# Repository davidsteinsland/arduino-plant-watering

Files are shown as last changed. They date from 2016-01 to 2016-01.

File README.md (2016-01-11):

Arduino Plant Watering
======================

A Real Time Clock controlled water pump regulator, for watering your plants.
The LCD have four available states:

- Initial state: Shows the time and how many times the pump has ran
- Pump configuration: Configure how many seconds the pump will run
- Schedule configuration: Enable/disable the timer
- Alarm configuration: Configure the time between each watering (can be every minute; a specific minute every hour; or a specific time each day).

The internal software is using a mixture of the RTC module and AVR's Watchdog Timer to properly time the pump and the schedule.
A float switch is also connected to the circuit, allowing the pump to run if there is enough water. It will also cut-off the pump as soon
as float switch turns off.

The power supply is a 12v wall-wart that's fused with 50mA to Arduino and 5A to the pump.

The three buttons are regulated at 0V, 1V and 2V, and read using `A0`. The switches are debounced in software.

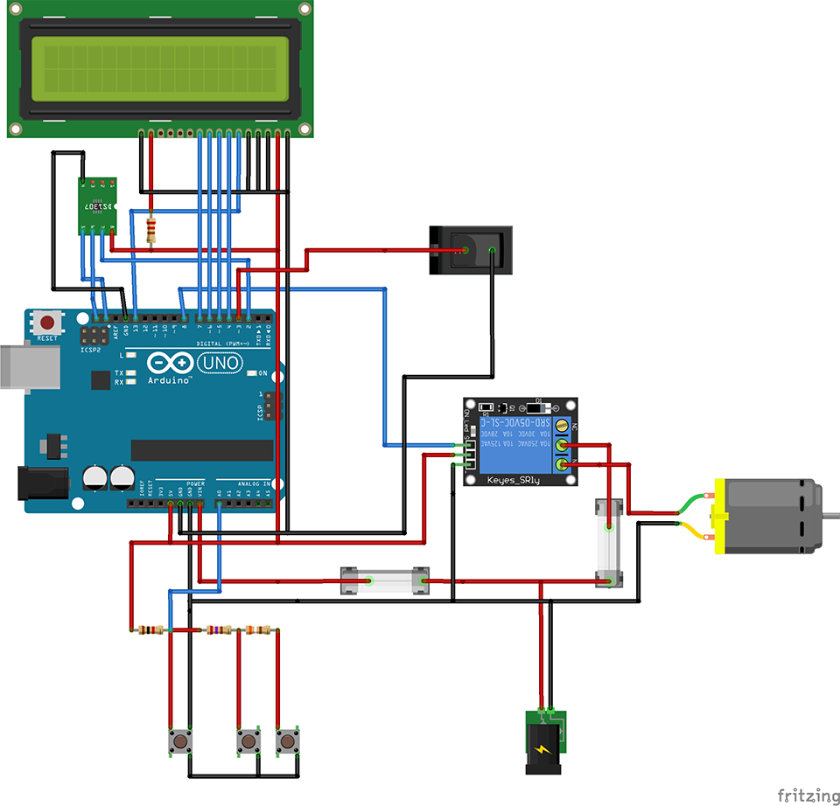
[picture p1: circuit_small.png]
Circuit


# Hardware

* [12V relay module](http://www.kjell.com/se/sortiment/el/elektronik/arduino/moduler/relamodul-for-arduino-p87878)
* [Water hose](http://www.biltema.no/no/Bil---MC/Bilreservedeler/Viskerutstyr/Spylerpumpe/Spylerpumpe-ovrig/Spylerslange-5-m-2000031910/)
* [Windshield washer pump](http://www.biltema.no/no/Bil---MC/Bilreservedeler/Viskerutstyr/Spylerpumpe/Spylerpumpe/Vindusspylerpumpe-universal-2000017965/)
* [12V power supply](http://www.biltema.no/no/Kontor---Teknikk/Batteri-og-Stromforsyning/Nettaggregat-og-ladere/Nettadapter-2000022525/)
* [16x2 LCD](http://hobbykomponenter.no/elektronikk/komponenter/display/lcd/16-and-215-2-lcd-display-blaa/)
* [DS3231 RTC module](http://hobbykomponenter.no/elektronikk/moduler/ds3231-rtc-modul/) (or similar)
* [Float switch](http://hobbykomponenter.no/elektronikk/sensorer/nivaasensor-sidemontert-flottr/)

## Additional

* Resistors
* Wires
* LEDs
* A switch button
* Free time.

# Future improvements

- Flowmeter: Configure the amount of water your want to be pumped, instead of pump time
- Hardware debouncing of buttons
- Noise reducing of water pump when it's active
- Status LEDs
- Bluetooth / integration with the nRF51 kit by Nordic Semiconductor.

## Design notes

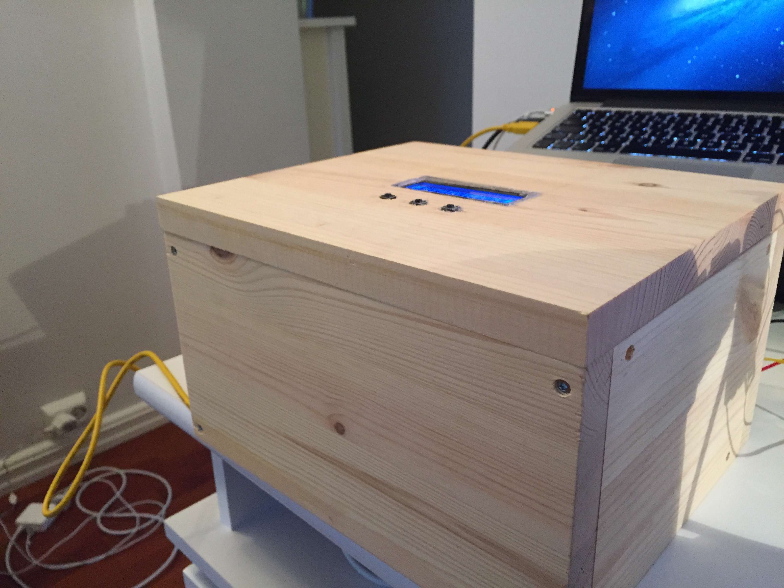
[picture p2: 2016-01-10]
photos/v2/box_side.jpg

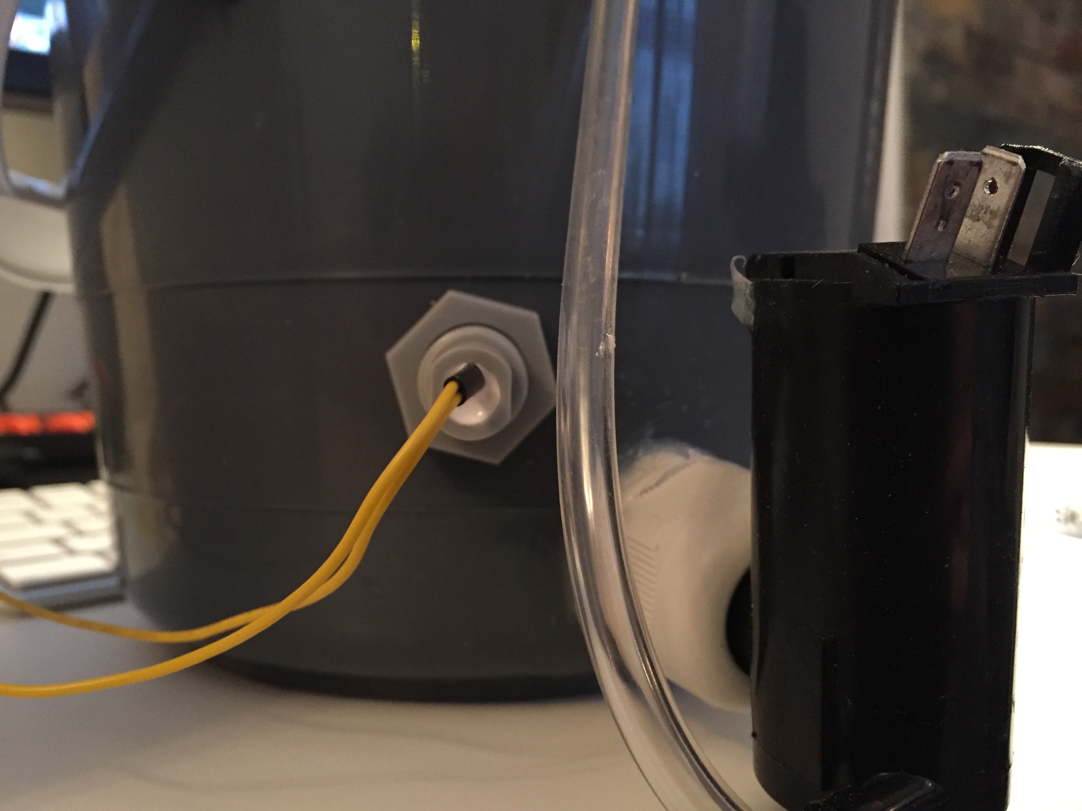
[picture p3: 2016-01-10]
photos/v2/bucket_pump.jpg

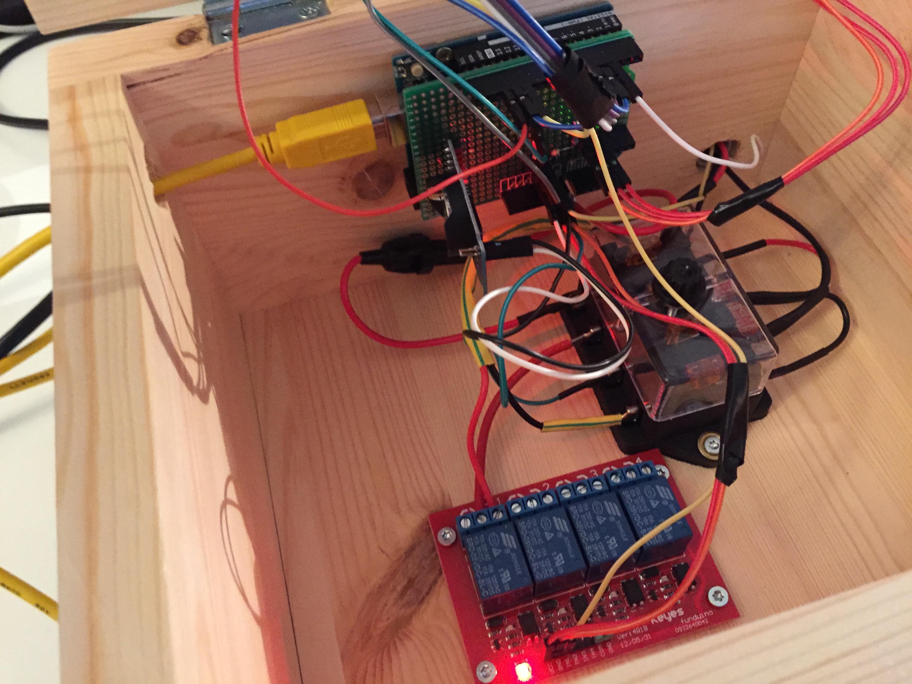
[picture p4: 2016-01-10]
photos/v2/inside_1.jpg

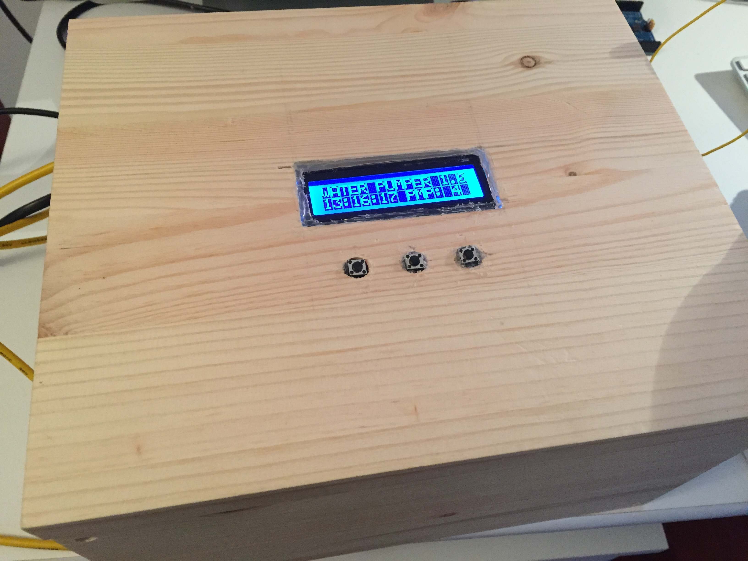
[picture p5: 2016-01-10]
photos/v2/box.jpg

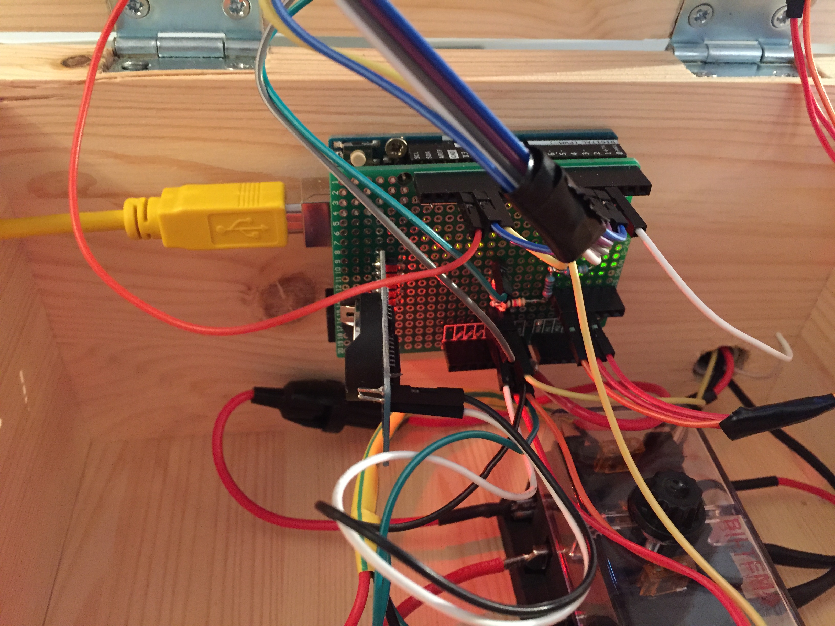
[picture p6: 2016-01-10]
photos/v2/inside_2.jpg

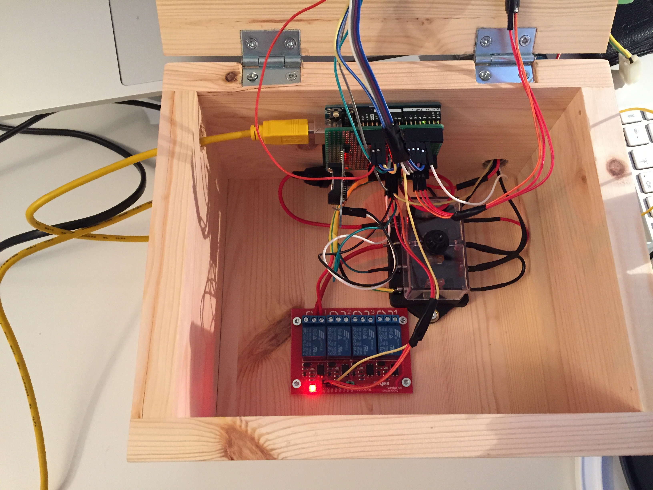
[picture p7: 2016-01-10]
photos/v2/inside_5.jpg

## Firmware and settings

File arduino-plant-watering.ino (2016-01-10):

#include <avr/wdt.h>

#include <LiquidCrystal.h>
#include <DS3232RTC.h>    //http://github.com/JChristensen/DS3232RTC
#include <Time.h>         //http://www.arduino.cc/playground/Code/Time
#include <Wire.h>         //http://arduino.cc/en/Reference/Wire (included with Arduino IDE)

#include "config.h"
#include "ds3232.h"
#include "buttons.h"
#include "lcd.h"
#include "frames.h"
#include "busy_wait.h"

pump_t pump = {
  .state = PUMP_OFF,
  .state_start = 0,
  .runtime = WATER_RUNTIME,
  .count = 0
};

void setup() {
  uint8_t arrow[8] = {
    0b00000,
    0b00100,
    0b00010,
    0b11111,
    0b00010,
    0b00100,
    0b00000,
    0b00000
  };
  lcd.createChar(0, arrow);
  lcd.begin(COLS, ROWS);

  lcd.print("WATER PUMPER 1.0");
  uint16_t _delay = 1000;
  uint16_t _char_delay = _delay / COLS;

  uint8_t i, j = 0;
  for (j = 0; j < COLS; ++j) {
    if (j > 0) {
      busyWait(_char_delay);
    }

    lcd.setCursor(0, 1);
    for (i = 0; i < j; ++i) {
      lcd.print('-');
    }
    lcd.write(byte(0));
   }

  setSyncProvider(RTC.get);
  if (timeStatus() != timeSet) {
     lcd.print("Error: Invalid time status");
  }

  delay(1000);

  /* configure our buttons, according to:

            [analog A0]
                |
  5v --> [1kΩ] -+--> [270Ω] +-> [390Ω] +
                |           |          |
                v           v          v
             [ btn ]     [ btn ]    [ btn ]
                |           |          |
  gnd <---------+-----------+----------+
  */
  button_init(1000, 0);
  button_init(1000, 270);
  button_init(1000, 270 + 390);

  readAlarm(ALARM_2, &alarm2_def);

  // clear alarm flags
  RTC.alarm(ALARM_1);
  RTC.alarm(ALARM_2);

  RTC.squareWave(SQWAVE_NONE);

  current_time = now();

  RTC.setAlarm(ALM1_EVERY_SECOND, 0, 0, 0, 0); // every second
  //RTC.setAlarm(ALM2_MATCH_MINUTES, 0, 0, 0, 0); // every zero-th minute
  RTC.alarmInterrupt(ALARM_1, true);
  //RTC.alarmInterrupt(ALARM_2, true);

  pinMode(RTC_INT_PIN, INPUT_PULLUP);
  attachInterrupt(digitalPinToInterrupt(RTC_INT_PIN), alarmChange, FALLING);

  pinMode(FLOAT_SWITCH_INT_PIN, INPUT_PULLUP);
  attachInterrupt(digitalPinToInterrupt(FLOAT_SWITCH_INT_PIN), floatSwitchInterrupt, CHANGE);

  pinMode(PUMP_PIN, OUTPUT);
  digitalWrite(PUMP_PIN, LOW);
}

void pump_on() {
  if (digitalRead(FLOAT_SWITCH_INT_PIN) == FLOAT_SWITCH_OFF) {
    return;
  }

  pump.state = PUMP_ON;
  pump.state_start = millis();
  pump.count++;
  digitalWrite(PUMP_PIN, HIGH);

  /* configure watchdog to 1 second */
  watchdog_init(WDTO_1S);
}

void pump_off() {
  wdt_disable();

  digitalWrite(PUMP_PIN, LOW);
  pump.state = PUMP_OFF;
  pump.state_start = millis();
}

uint16_t get_pump_count() {
  return pump.count;
}

uint16_t get_pump_runtime() {
  return pump.runtime;
}

void set_pump_runtime(uint16_t runtime) {
  pump.runtime = runtime;
}

/*
  RTC Alarm ISR
 */
void alarmChange() {
  alarmCalled = 1;
}

/*
  Float switch ISR
 */
void floatSwitchInterrupt() {
  if (digitalRead(FLOAT_SWITCH_INT_PIN) == FLOAT_SWITCH_OFF && pump.state == PUMP_ON) {
    pump_off();
  }
}

void watchdog_init(uint8_t mask) {
  /* Clear the reset flag. */
  MCUSR &= ~(1 << WDRF);

  /* In order to change WDE or the prescaler, we need to
  * set WDCE (This will allow updates for 4 clock cycles).
  */
  WDTCSR |= (1<<WDCE) | (1<<WDE);

  /* set new watchdog timeout prescaler value */
  WDTCSR = mask;

  /* Enable the WD interrupt (note no reset). */
  WDTCSR |= _BV(WDIE);
}

/*
  Watchdog ISR
 */
ISR(WDT_vect) {
  if ((millis() - pump.state_start) >= pump.runtime) {
    pump_off();
  }
}

void loop() {
  if (alarmCalled) {
    alarmCalled = 0;
    if (RTC.alarm(ALARM_1)) {
      handle_alarm1();
    }

    if (RTC.alarm(ALARM_2) && is_alarm_active(ALARM_2)) {
      handle_alarm2();
    }
  }

  switch (get_active_frame()) {
    case FRAME_0:
      /* root frame */
      frame0();
    break;

    case FRAME_1:
      /* menu frame */
      frame1();
    break;

    case FRAME_2:
      /* menu option frame */
      frame2();
      break;

    case FRAME_3:
      frame3();
      break;
  }

  set_prev_frame(get_active_frame());

  if (get_next_frame() != -1) {
    set_active_frame(get_next_frame());
    set_next_frame(-1);
    set_last_draw();
  }
}

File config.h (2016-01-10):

#ifndef TIMER_DISPLAY_H
#define TIMER_DISPLAY_H

/*
LiquidCrystal::LiquidCrystal(uint8_t rs, uint8_t enable,
           uint8_t d0, uint8_t d1, uint8_t d2, uint8_t d3,
           uint8_t d4, uint8_t d5, uint8_t d6, uint8_t d7)
*/

#define COLS 16
#define ROWS 2

#define LCD_PIN_RS 13
#define LCD_PIN_E 12
#define LCD_PIN_D0 11
#define LCD_PIN_D1 10
#define LCD_PIN_D2 9
#define LCD_PIN_D3 8
#define LCD_PIN_D4 7
#define LCD_PIN_D5 6
#define LCD_PIN_D6 5
#define LCD_PIN_D7 4

#define PUMP_PIN 8
#define RTC_INT_PIN 2
#define FLOAT_SWITCH_INT_PIN 3
#define BUTTONS_PIN A0

#define FRAME_0 0
#define FRAME_1 1
#define FRAME_2 2
#define FRAME_3 3

#define TIMER_STATE_SCHEDULE 0
#define TIMER_STATE_HOUR 1
#define TIMER_STATE_MINUTE 2
#define TIMER_STATE_SECOND 3
#define TIMER_STATE_CONFIRM 4
#define TIMER_STATE_SET 5

#define PUMP_SET_TIME 0
#define PUMP_TIME_CONFIRM 1

#define FLOAT_SWITCH_ON 0
#define FLOAT_SWITCH_OFF 1

#define WATER_MIN_RUNTIME 1000
#define WATER_MAX_RUNTIME 10000
#define WATER_RUNTIME 5000


#define PUMP_OFF 0
#define PUMP_ON 1

typedef struct {
  uint8_t state;
  unsigned long state_start;
  uint16_t runtime;
  uint16_t count;
} pump_t;

volatile time_t current_time;

typedef struct {
  uint8_t alarm;
  ALARM_TYPES_t type;
  uint8_t hours;
  uint8_t minutes;
  uint8_t seconds;
} alarm_t;

volatile uint8_t alarmCalled = 0;

/*LiquidCrystal lcd(LCD_PIN_RS, LCD_PIN_E, LCD_PIN_D0, LCD_PIN_D1, LCD_PIN_D2,
  LCD_PIN_D3, LCD_PIN_D4, LCD_PIN_D5, LCD_PIN_D6, LCD_PIN_D7);*/

LiquidCrystal lcd(LCD_PIN_RS, LCD_PIN_E, LCD_PIN_D4, LCD_PIN_D5, LCD_PIN_D6, LCD_PIN_D7);

alarm_t alarm2_def;

void pump_on();
void pump_off();
uint16_t get_pump_count();
uint16_t get_pump_runtime();
void set_pump_runtime(uint16_t);


#endif

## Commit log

2015-11-21 Added program
    [circuit.fzz]
2015-11-22 Updated circuit
    [circuit.fzz]
2015-11-30 Moved code to header files; added float switch
2015-12-01 Moved file to be compatible with Arduino IDE
2015-12-01 Fixed debounce to micros
    [arduino-plant-watering.ino]
2015-12-01 If we cut-off pump in the middle of running, make sure it starts again
2016-01-10 Allow configurable runtime of pump
